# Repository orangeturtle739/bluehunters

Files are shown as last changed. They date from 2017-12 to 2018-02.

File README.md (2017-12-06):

---
title: 'Blue Hunters: Bluetooth RSSI Locator Robots'
subtitle: '_ECE 4760, Fall 2017_'
author:
  - Jacob Glueck ([jng55](mailto:jng55@cornell.edu))
  - Jane Du ([zd53](mailto:zd53@cornell.edu))
  - Justin Cray ([jgc232](mailto:jgc232@cornell.edu))

date: December 6, 2017
---

## Introduction
We built 2 small cars which used Bluetooth Received Signal Strength Indicator (RSSI) measurements to navigate towards a stationary base station.
The cars and base station used a Bluetooth Low Energy (BLE) 4.0 module to take the measurements and a PIC32MX250 microcontroller. The cars also used a 3 axis magnetometer as as compass in order to reliably turn, as well as 2 micro 9 g servos to drive.
Each unit was powered with 3 AA batteries.
Finally, the chassis and wheels of each car were 3D printed.

### Video

<iframe width="560" height="315" src="https://www.youtube.com/embed/g5H4cLJBA_Q?rel=0" frameborder="0" gesture="media" allow="encrypted-media" allowfullscreen></iframe>

## Design
<!-- Explain the approach you used for both software and hardware aspects of the assignment.
Be sure to include the design of tests whose outcome are convincing to the reader
(or to the instructor in the lab) that the requirements of the assignment have been met. -->
<!-- High level design:
rationale and sources of your project idea
background math
logical structure
hardware/software tradeoffs
Relationship of your design to available IEEE, ISO, ANSI, DIN, and other standards.
Discuss existing patents, copyrights, and trademarks which are relevant to your project.
Program/hardware design:
program details. Could someone else build this based on what you have written?
hardware details. Could someone else build this based on what you have written?
Be sure to specifically reference any design or code you used from someone else.
Things you tried which did not work -->

### Chassis

The robots are made from 4 3D printed pieces: 2 wheels, the frame, and the caster in the back.
The servos, a 3 AA battery holder, and a perfboard containing all the circuitry are mounted directly to the frame.

The robots where designed in [OpenSCAD](http://www.openscad.org/), and their source code is available in [our git repository](https://github.com/orangeturtle739/bluehunters/tree/master/cad) and [below](#appendix-b-source-listing).
There are three files, [`frame.scad`](generated/frame.scad.html), [`drag.scad`](generated/drag.scad.html), and [`wheel.scad`](generated/wheel.scad.html), for each of the three parts. The main modules are defined in [`main.scad`](generated/main.scad.html), and the other files just instantiate them. The following renderings show each part:

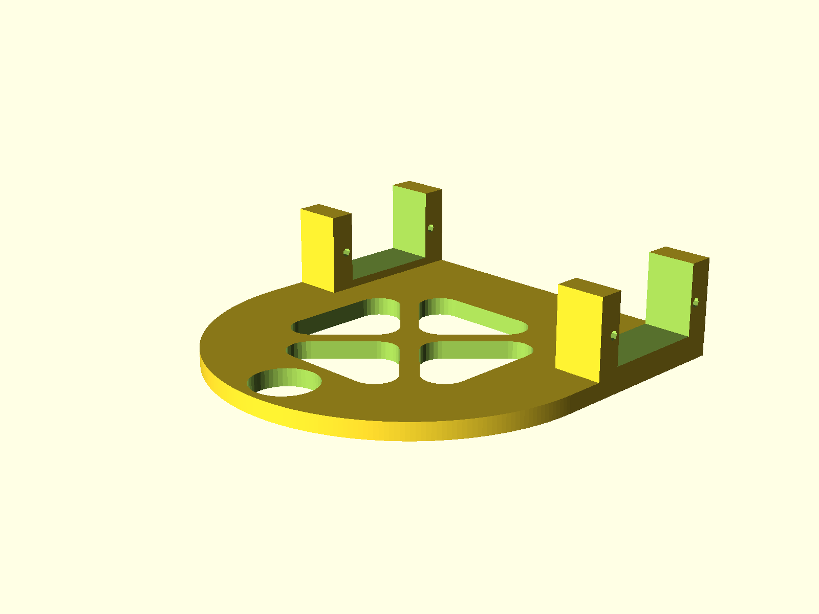
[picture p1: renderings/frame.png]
Robot chassis


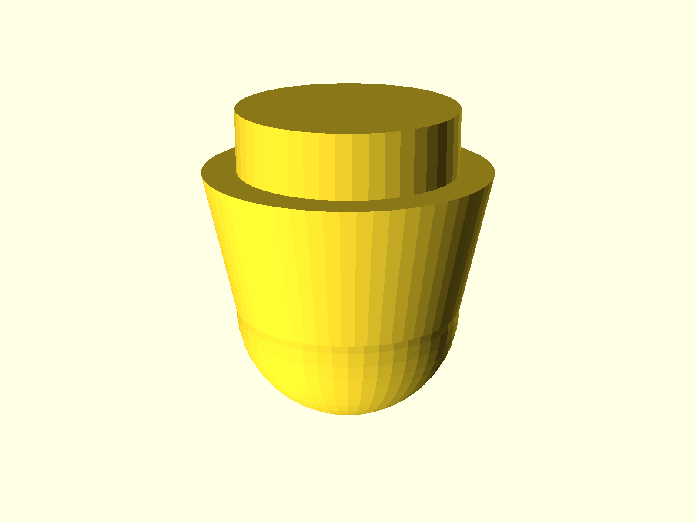
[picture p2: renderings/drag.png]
Caster wheel on back of robot


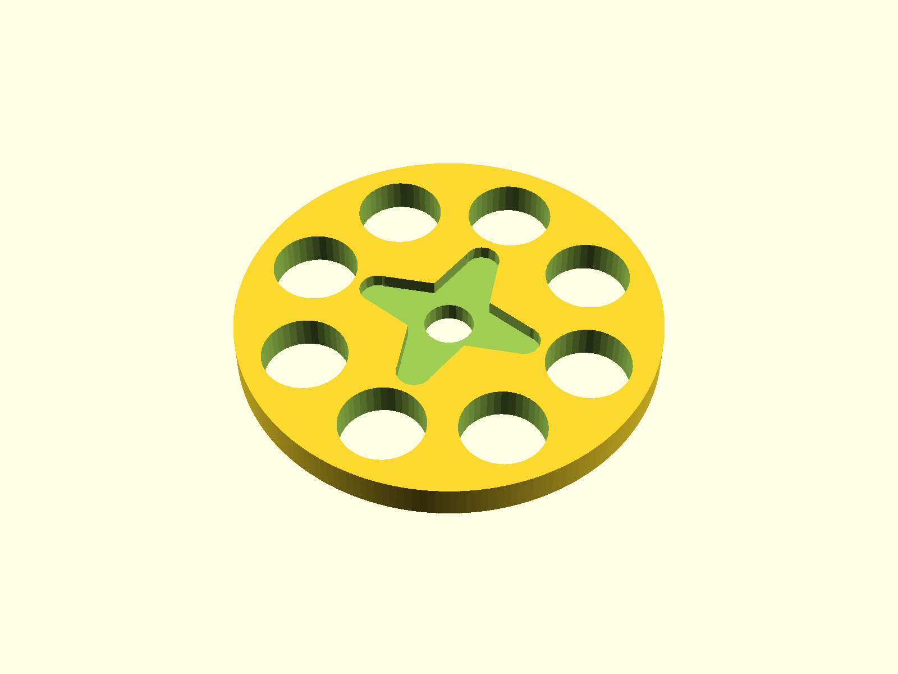
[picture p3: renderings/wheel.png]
Robot wheel


The parts were printed in ABS using [Maker Select 3D Printer v2](https://www.monoprice.com/product?c_id=107&cp_id=10724&cs_id=1072403&p_id=13860&seq=1&format=2) printers. All parts were printed
with a layer height of 0.3 mm, as there was no need for a smooth finish or high tolerances. The parts where sliced with [Cura](https://ultimaker.com/en/products/ultimaker-cura-software).

### Pictures

Full system (base station and 2 robots):

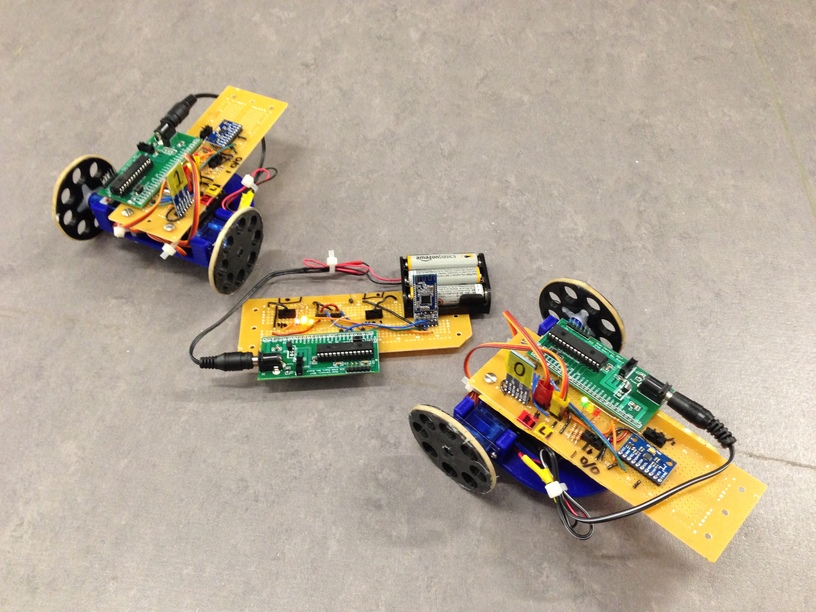
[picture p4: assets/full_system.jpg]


Multiple views of the robots:

------------------------------ ------------------------------
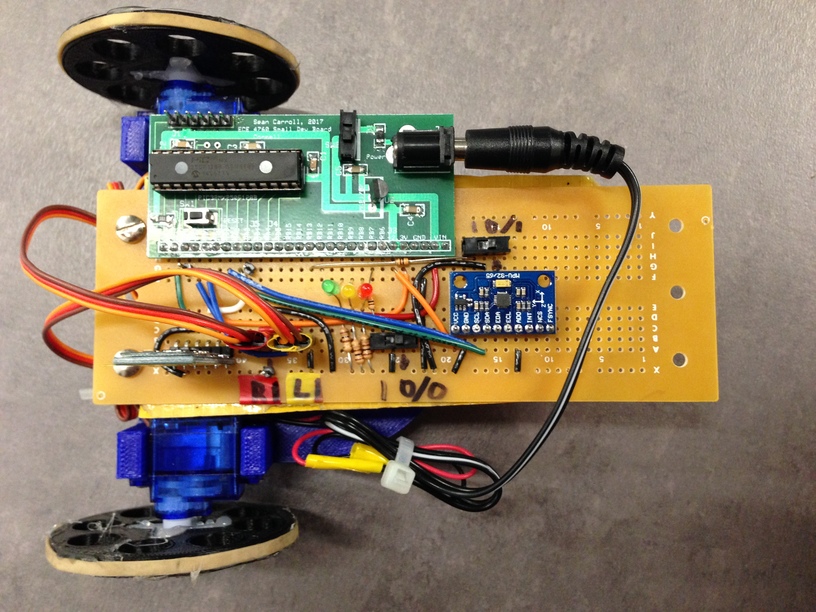
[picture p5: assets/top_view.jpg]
Top view
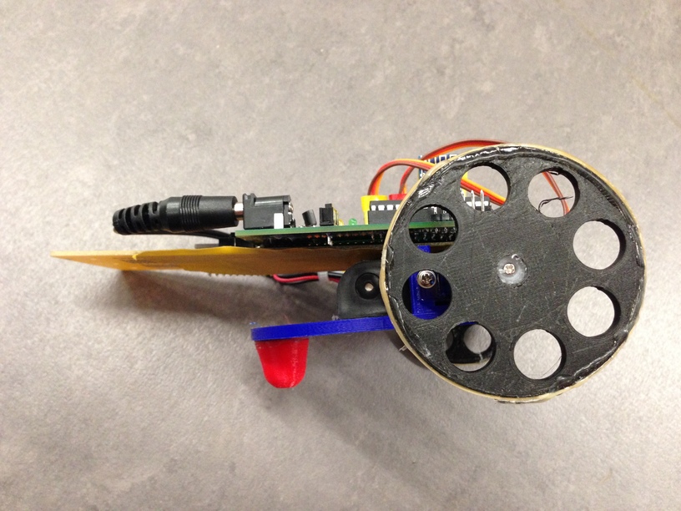
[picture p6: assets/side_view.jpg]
Side view
      
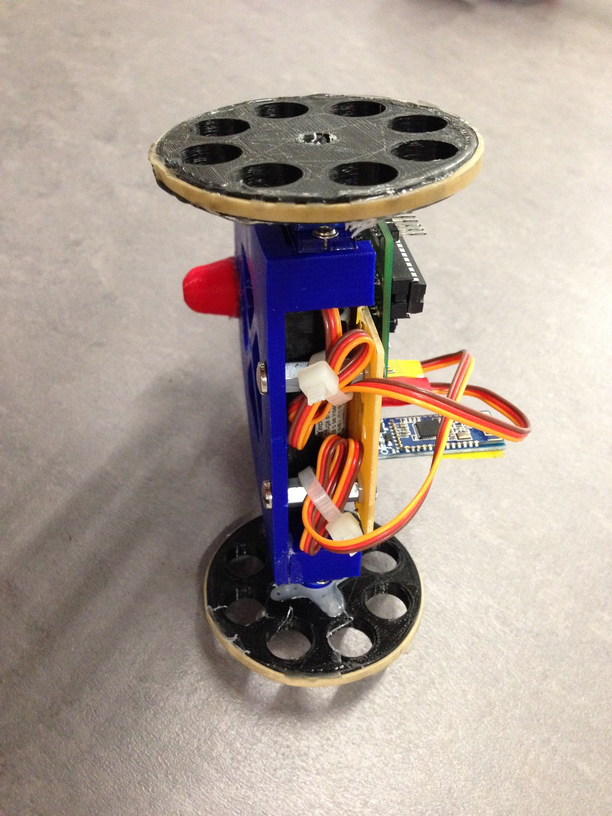
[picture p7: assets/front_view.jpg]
Front view
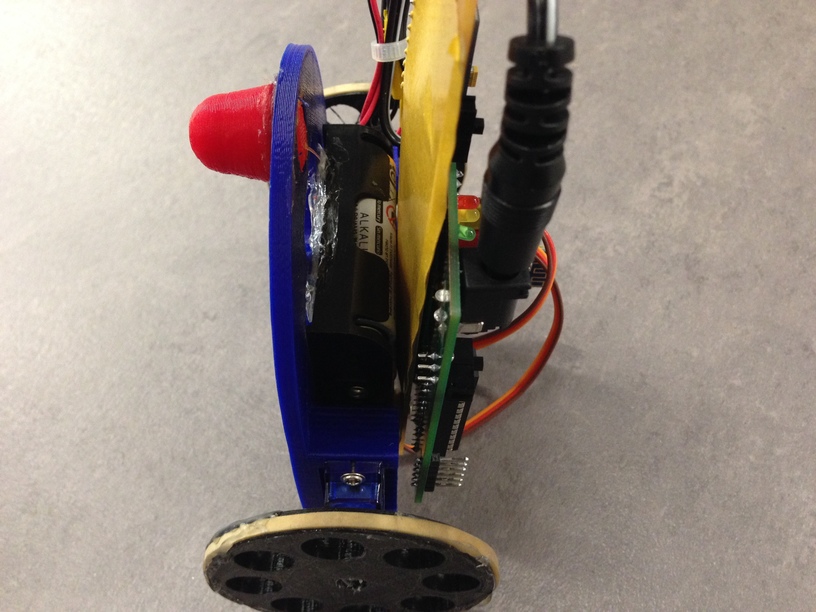
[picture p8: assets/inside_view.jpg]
Inside
  
------------------------------ ------------------------------

### Electronics

#### Bluetooth modules

The HM-10 bluetooth modules we bought off Ebay were fakes: they were not made by Jnhuamao [^china], and did not come with genuine Jnhuamao firmware.
However, they did have real TI CC2541 chips.
We realized they were fakes when they did not behave according to the Jnhuamao data sheet (see [the data sheets section](#data-sheets)).
Luckily, the hardware on the fake chips is the same as that of the genuine chips, minus an external crystal, and the genuine firmware checks for the presence of the crystal, and works even without it. [^arduinoforums]
As such, we reprogrammed the chips with the genuine firmware according to an [Arduino forum post](http://forum.arduino.cc/index.php?topic=393655.msg2709528#msg2709528):

1.  We soldered wires to the programming pins on the breakout boards, and connected those pins to an [Arduino Teensy 3.2](https://www.pjrc.com/teensy/teensy31.html).
    We chose a Teensy because it is 3.3 V as opposed to 5, which would damage the 3.3 V CC2541.

    The pins were connected as follows:

      | Name          | CC2541 Pin | Arduino Pin |
      | ------------- | ---        | ----------- |
      | `DEBUG_CLOCK` | 7          | 5           |
      | `DEBUG_DATA`  | 8          | 6           |
      | `RESET_N`     | 11         | 4           |

    The layout of the HM-10 board is:

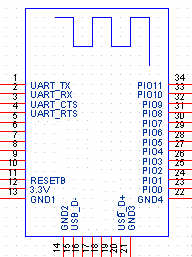
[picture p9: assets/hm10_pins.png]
    
2.  We uploaded the [`CCLoader.ino` sketch](https://github.com/RedBearLab/CCLoader/blob/master/Arduino/CCLoader/CCLoader.ino) to the Arduino.
3.  Finally, we ran (in a Windows virtual machine) [`CCLoader.exe`](https://github.com/RedBearLab/CCLoader/tree/master/Windows).
    This program takes 3 arguments:
    ```bash
    CCLoader.exe <COM Port> <Firmware.bin> 0
    ```
    The firmware file came from the same Arduino form post, and can be found [here](http://forum.arduino.cc/index.php?action=dlattach;topic=393655.0;attach=183702).

There is also an excellent [YouTube video](https://www.youtube.com/watch?v=ez3491-v8Og), which explains the firmware flashing process.

After flashing genuine firmware onto the chip, the next step was to update the firmware to the latest version.
The firmware flashed onto the board was version 540, but Jnhuamao had (at the time we did this project) [released version 603](http://www.jnhuamao.cn/rom/HMSoft-10-2541-V603.zip). [^firmware]
They also provide [instructions on how to upgrade the firmware](http://www.jnhuamao.cn/HowToUpgradeFirmware_en.zip). The basic process is:

1.  Connect the HM-10 module to a computer using a 3.3 V FTDI to USB adapter.
    Then, use PUTTY to establish a serial session (9600 baud, 8N1).
    Send the chip `AT`; if it is connected properly, it will respond with `OK`.
2.  Send the chip `AT+SBLUP` to put it in firmware update mode.
    It will respond with `OK+SBLUP`. Terminate the PUTTY session.
3.  Run the `HMSoft.exe` program distributed in the firmware update download.
    We ran it in a Windows virtual machine because we did not trust it.
4.  Select the proper port and firmware file using the software, and hit "Load Image".
    The software should handle the rest!
5.  To make sure it worked, establish a serial connection again using PUTTY.
    Send `AT+VERS?` to query the chip for version information.

[^china]: Jnhuamao is the company which makes the HM-10 module, along with other Bluetooth modules. Their English website is: <http://www.jnhuamao.cn/bluetooth.asp?id=1>.
[^arduinoforums]: <http://forum.arduino.cc/index.php?topic=393655.msg2709528#msg2709528>.
[^firmware]: Jnhuamao's firmware download page <http://www.jnhuamao.cn/download_rom_en.asp?id=1#>.

### Software

The robots were programmed in C, using the [MPLAB X IDE](http://www.microchip.com/mplab/mplab-x-ide) v4.0, with the [XC32](http://www.microchip.com/mplab/compilers) v1.4 compiler and the [PIC 32 Legacy Peripheral Library (plib)](http://www.microchip.com/SWLibraryWeb/product.aspx?product=PIC32%20Peripheral%20Library). The full source code is available in [our git repository](https://github.com/orangeturtle739/bluehunters/tree/master/ble.X) and [below](#appendix-b-source-listing). The code is divided into 5 main units:

*   [`ble.c`](generated/ble.c.html): contains all the functions for interacting with the BLE device over UART.
*   [`imu.c`](generated/imu.c.html): contains all the functions for interacting with the IMU (which contained the magnetometer) over I2C.
*   [`servo.c`](generated/servo.c.html): contains all the functions for interacting with the servos using PWM.
*   [`main.c`](generated/main.c.html): the main code.
*   [`pt_cornell_1_2_2.c`](generated/pt_cornell_1_2_2.c.html): contains the functions which were originally declared in the protothreads header file.
    However, since they were in the header file, if multiple source files included the header file, there would be linking errors due to duplicate definitions of symbols.
    Moving the protothreads definitions to a separate file resolved this issue.

#### BLE

The BLE module used UART, at 9600 baud 8N1. We used `UART1` on the PIC for communicating with the BLE module, and used `UART2` for communicating with the computer (for debugging).
The BLE files define a series of macros and `PT_THREAD` functions for printing characters and reading lines in a non-blocking fashion using protothreads. All of the `PT_THREAD` functions can be spawned with `PT_SPAWN` to run them.

The [`main.c`](generated/main.c.html) file contains a thread which does all the communication with the Bluetooth chip using these functions. The commands it sends to the chip are:

*   `AT+RESET`: resets the chip to ensure it is in a clean state before receiving other commands.
*   `AT+IBEA1`: enables the iBeacon functionality of the chip (sets it to 1; `AT+IBEA0` would disable it by setting it to 0).
    This allows the chip to be found with an RSSI scan.
    After setting the value, we query it with `AT+IBEA?` and send the result over the other serial port to a computer for debugging.
*   `AT+ROLE0` or `AT+ROLE1`: sets the role to either peripheral (0) or central (1).
    The base station is set to peripheral, and the 2 robots are set to central.
    Peripheral means the device will respond in inquiries from a central device.
    This allows it to be discovered during an RSSI scan.
    After setting the value, we query it with `AT+ROLE?` and send the result over the other serial port to a computer for debugging.
*   `AT+IMME0` or `AT+IMME1`: sets the work state of the device to either actively listening for Bluetooth signals (0), or only acting when it receives a serial command (1).
    Once again, the base station is set to 0: it needs to listen for signals and respond.
    The robots are set to 1, as the chips need to initiate scan requests when they receive the command over serial.
    After setting the value, we query it with `AT+IMME?` and send the result over the other serial port to a computer for debugging.
*   `AT+NAME%s`: sets the name of the chip (which is visible when scanning) to `%s` (For example, `AT+NAMEPIRATE` names the chip `PIRATE`).
    We give all the chips unique names to make debugging easier.
    After setting the value, we query it with `AT+NAME?` and send the result over the other serial port to a computer for debugging.
*   `AT+SHOW3`: configures the device to advertise both its name and RSSI when scanning.
*   `AT+ADDR?`: queries the device for its hardware address. We recorded the hardware device of each chip, as when doing RSSI scans, the results are reported by hardware address.
*   `AT+DISI?`: performed only on the robots, causing a discovery scan. The result of the scan is a bunch of lines of the form:
    ```
    OK+DISC:00000000:00000000000000000000000000000000:0000000000:6832A3801EBE:-080
    ```
    The second to last token, `6832A3801EBE`, is the hardware address of the discovered device, and the last token, `-080`, is the measured RSSI.
    The chip will transmit a line for each device it finds ("line" is a misnomer as it does not separate them with any characters), followed by `OK+DISCE`.

One interesting thing to note about the chip is that commands do not have to end with newlines or carriage returns. However, if sent, the chip will ignore them.

#### IMU
The PIC commmunicates with the IMU via I2C. The IMU includes a breakout board for the QFN MPU-9250 module, which itself includes 2 dies. One contains the 3-axis gyroscope and 3-axis accelerometer, which were not used in this project, and the other die is the AK8963 3-axis magnetometer (compass).

It is connected to the rest of the MPU module via an auxillary I2C bus, so it is not connected to the MPU's  main I2C bus by default. While the accelerometer and gyroscope registers can be read after powering up the IMU, the compass also needs pass-through mode to be enabled on the IMU to make it an accessible slave on the I2C bus.

Some useful functions as defined in [`imu.h`](generated/imu.h.html) are described below:

*   `void imu_init()`: Initializes the MPU-9250, including configuring the chip to allow reading the compass.
*   `int imu_get_heading()`  Returns the heading of the robot as a value between -180 and 180.
    The compasses were not completely calibrated to find magnetic north; it only ensures angles are correct relevant to past headings.
*   `void imu_mag_read_data(int * destination)` Fetches compass readings; saves register values into `destination` in the form `[x, y, z]`.
*   `int angle_diff(int source, int target)` Gets the difference between two angles in degrees to account for discontinuity between -180 and 180 degrees.
*   `int degree(int deg)`: Offsets degree values so that they fall within the range -180 to 180 degrees.

Initializing the IMU involves opening the I2C module, and then configuring the IMU.

1.  We open the `I2C2` module; `I2C1` uses pins already used by the connections to the Bluetooth module.
    We open it with the baud rate generator value `BRG = (Fpb / 2 / baudrate) - 2 = 4e7 / 2 / 4e5 - 2 = 48`, as specified for `OpenI2C2()` in the [peripheral libraries](#references).
2.  Pass through is enabled, interrupts for data ready are enabled, the IMU as an I2C master function is disabled, and the sensor is powered up.

This enables the PIC to talk to the AK8963. The AK8963 has several modes of operation, and the chip must be set to power-down mode before switching to other modes. We read compass values with single measurement mode, as specified below:

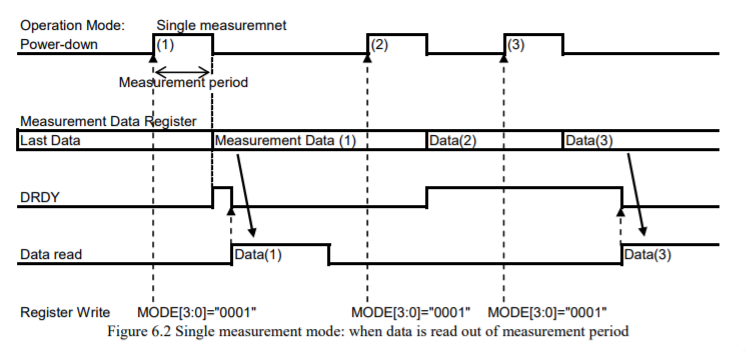
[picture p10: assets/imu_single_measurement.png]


1.  Set the compass to single measurement mode in 14 bit resolution.
2.  Read the 6 data registers (X low, X high, Y low, Y high, Z low, Z high)
3.  Read the Status 2 register to check for magnetic sensor overflow. Without reading this register, the read is not considered complete and further reads will fail.
4.  Wait; if the IMU is read too frequently, it will not have enough time to take measurements.

Additional helper methods used in I2C were defined in [`imu.c`](generated/imu.c.html). These are largely based on the files from the [self-balancing robot](#code-and-designs-borrowed-from-others).

*   `char i2c_read_device(char device, char address)` Reads the data from a single register at `address`
*   `void i2c_write_byte(char device, char address, char data)` All configurations used in this project involved writing single bytes of data.
*   `void i2c_wait(int cnt)` Writes 2 nops; reads require time to return a value, and calling reads consecutively.

In order to calibrate the compass, the robots spun in place when powered on. They recorded the maximum and minimum values for each axes, and used that data to scale and center the magnetometer readings.

#### Servos

For the drive systems, we used the FS90R servos. These servos are continuous rotation servos with a stall torque of 1.5 kg-cm. Continuous rotation servos operate based on PWM duty cycle; since servos operate at a pulse width of 1 to 2 ms out of 20 ms, we used a timer with a prescaler of 32 and a maximum count of 25600, and set the pwm at numbers ranging from 1280 to 2560 (corresponding to the right pulse width).

A 50% duty cycle means the servos are still. A less than 50% duty cycle means the servo turns clockwise and a greater than 50% duty cycle means the servo turns counter-clockwise. To implement the PWM, we use the output capture on the PIC. We set the duty cycle using the built in timers. We set a max and min duty cycle value which were experimentally derived. The middle point is the average of the two. Tank drive is used to control the system where both wheels are driven forward or point turns where one wheel is turned in one direction and one is turned in the other direction. 

#### Protothreads

While the provided protothreads library was very helpful, it did not work correctly when used in multiple compilation units.
The reason for this was that it defined variables and functions in the header file, so if multiple source files included [`pt_cornell_1_2_2.h`](generated/pt_cornell_1_2_2.h.html), linking would fail with duplicate symbol definitions.
Furthermore, if multiple files included [`config_1_2_2.h`](generated/config_1_2_2.h.html), linking would fail with the obscure error:
```
section `.config_BFC00BF4' will not fit in region `config2'
```
This happened because if multiple compilation units included `#pragma config` directives (which they did by including a `#include "config_1_2_2.h"` directive), then the linker would try to assign too many symbols to the configuration region.

The fix to this was twofold:

1.  We modified protothreads to have both a header and source file, with definitions only in the source file.
1.  We only included [`config_1_2_2.h`](generated/config_1_2_2.h.html) in the main C file, and moved all macro definitions to the protothreads header.

The updated versions of protothreads can be found in [Appendix B](#appendix-b-source-listing).

#### Gradient descent

The algorithm for deciding what path to follow is a basic version of gradient descent. The following image represents the decision-making state machine, where the starting state is **Measure rssi twice, take average**.

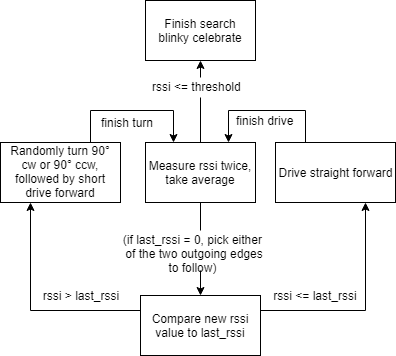
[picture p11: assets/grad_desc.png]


We also implemented and tested the following improved version that allows for correction; a car that has just moved forward and detected a weakened signal does not know whether the beacon to its left or right. If after turning, the signal is still weaker, it has picked the wrong turn. This decision process corrects this (same starting state: **Measure rssi twice, take average**):

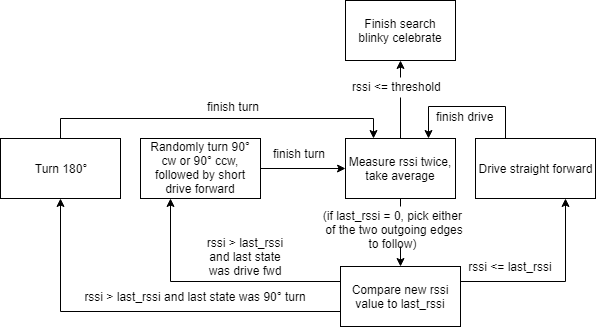
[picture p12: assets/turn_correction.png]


It did not prove much more accurate than randomized gradient descent, largely due to noisy readings from IMU and Bluetooth signal strength. As such, we used the simplified version.

### Testing

#### BLE

Once we flashed the Bluetooth chips with the proper firmware, we used the [LightBlue](https://itunes.apple.com/us/app/lightblue-explorer/id557428110?mt=8) app to test communications.
Using the app, we could discover the Bluetooth chips, and send and receive data.
By initially using a the iPhone app, which was known to work, we could debug the Bluetooth chips in isolation.
Once that worked, we had the chips communicate with each other.
Finally, we had the chips take RSSI measurements.

We also experimented with RSSI, as described in [results](#results). This data validated the effectiveness of RSSI as an approximate metric for distance measurement, though confirmed that it would be highly variable.

#### IMU
- Basic I2C: Basic testing was required to ensure I2C communication with the chip was working. This included testing the correctness of the I2C read and write functions (including the order of starts, restarts, and idles in accordance with the I2C protocol and the chip datasheets), as well basic parameters like the address of the MPU-9250 and its registers.
- Compass I2C: This was more complex, and mostly involved testing the usage of the modes of both the MPU-9250 (IMU module) and the AK8963 (the compass itself). Performance testing was also important here, as the compass would not allow rapid reads in quick succession; we inserted nops in the `imu_mag_read_data(int * destination)` for this reason.
- Compass calibration: We tested incrementally, first using hard-coded maximum and minimum observed values outputted from the IMU, and then with values taken from a self-calibration in which the robot would spin in a circle, and the PIC would record the largest and smallest values it saw on the X- and Y-axes.

#### Servos
We tested the functionality of servo code by testing individual functionality on both the hardware and software side. We tested the servo code in stages, first implementing control at a fixed speed and then implementing directional motion and lastly turning. This allowed us to verify our parts of the code and the functionality of the servos.

#### Whole system
- Some subsystem testing was required for the servo with the IMUs, for turning/driving straight with feedback. We debugged by reading in IMU values via UART and observing the robot's turns.
- We tested extensively with the beacon and two hunters in different environments. Most of our initial testing was in a large, open space with a few metal tables on the periphery. We later tested in the lab in the Digital Lab (Phillips 238), and in the hallway where our demo took place. The confined space of the inside of the lab and hallway, as well as the presence of more reflective bodies (metal doors, tables, people) negatively impacted the performance of our hunters, and it was necessary to recalibrate the hunters to work better in the demo environment.

## Results
<!-- How fast was it? How accurate was it? What were the error ranges? -->
<!--
Results of the design:
This is the section which is most often lacking in student projects. Be specific!
If you took calibration data, then show it!
If you have images or video, include it.
speed of execution (hesitation, filcker, interactiveness, concurrency)
Be quantitative. Show graphs!
accuracy (numeric, music frequencies, video signal timing, etc)
Be quantitative. Show graphs!
how you enforced safety in the design.
interference with other people's designs (e.g. cpu noise, RF interference).
usability by you and other people (perhaps with special needs). -->

In most cases, at least 1 of the 2 robots successfully made it to the base station. However, it was not as reliable as we initially hoped. One of the main reasons for this was the noise in RSSI measurements.

We expected that RSSI would vary with distance according to the following relation:

$\text{RSSI} = A - 10 n \log(d)$

where $A$ and $n$ are RF propagation parameters in dBm, $d$ is distance in meters, and RSSI is the measured RSSI in dBm. [^signalstrength]
We experimented with RSSI measurements to determine how well they worked by taking 2 Bluetooth modules, and measuring the RSSI while changing the distance between them.
One remained stationary on the floor and the other was moved away from it 1 floor tile (each floor tile is a 1 foot square) at a time.
At each point, we took 3 RSSI measurements and averaged them. The graph below displays the results:

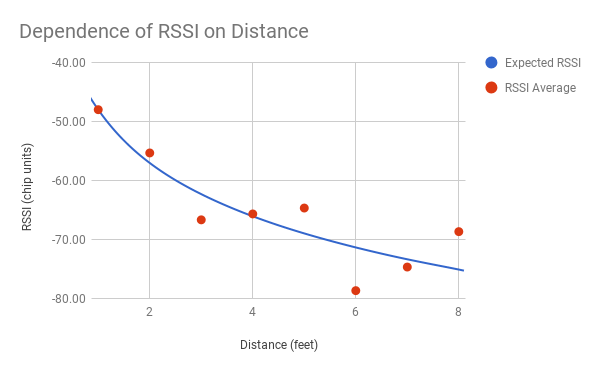
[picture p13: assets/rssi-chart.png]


While the chip reported RSSI in units proportional to dBm, and we measured distances in feet, not meters, we could still use the above formula without worrying about unit conversions.
The constants $A$ and $n$, provided we determined them empirically based on the data, would encode the conversions.
As such, we fit the data using the above formula with $A=-48$ and $n=3$, resulting in the blue curve above.
While the general shape of the curve matches, there is significant noise in the averaged RSSI data.
Furthermore, when we tried to reproduce the measurements, we could not do so precisely -- it seemed to even depend on where our feet where! See [Appendix B](#rssi-data) for the source data for the table.

Despite how noisy the RSSI measurements where, the robots were still able to perform a reasonably accurate gradient descent. In most cases, at least one of the 2 robots would find the beacon in a matter of minutes.

[^signalstrength]: L. Peneda, A. Azenha and A. Carvalho, "Trilateration for indoors positioning within the framework of wireless communications," 2009 35th Annual Conference of IEEE Industrial Electronics, Porto, 2009, pp. 2732-2737.

    doi: 10.1109/IECON.2009.5415423

    URL: <http://ieeexplore.ieee.org/stamp/stamp.jsp?tp=&arnumber=5415423&isnumber=5414636>

## Conclusions
<!-- Useability, what you might have done differently, etc. Any comments concerning the assignment, including suggestions for improvement, excuses, and complaints. -->
<!-- Conclusions:
Analyse your design in terms of how the results met your expectations. What might you do differently next time?
How did your design conform to the applicable standards?
Intellectual property considerations.
Did you reuse code or someone else's design?
Did you use code in the public domain?
Are you reverse-engineering a design? How did you deal with patent/trademark issues.
Did you have to sign non-disclosure to get a sample part?
Are there patent opportunites for your project?
Are there publishing opportunities for your project?
Ethical considerations. Refering to the IEEE Code of Ethics, specifically explain how decisions you made or actions you took in this project were consistent with this Code of Ethics. I expect at least 200 words on this topic. A bulleted list will not be acceptable. -->

This assignment was an interesting exploration into short-range distance determination using Bluetooth, a generally unconventional approach. We were warned beforehand about the difficulties in using Bluetooth RSSI, a measurement particularly susceptible to multipath interference, as a distance sensor -- both in the papers and reference materials researched before implementation, as well as by course staff in the early stages of our project. We worked with the course staff to simplify and stratify our project into workable milestones. Our final project is a reduced version of our original plan.

Our hunting bots worked reliably when they stayed within roughly 1 m of the beacon. After this, they entered the land of shallow gradients: the signal strength from the beacon (already noisy) would not change very much, and often only due to noise. The hunting bots normally could never recover from this. Our bots also worked better in larger, more open spaces, preferably without metal structures like tables or doors nearby. Both of these are reasonable given the operating range of BLE 4.0.

We reused some of the code from the [Self-Balancing Robot](https://people.ece.cornell.edu/land/courses/ece4760/FinalProjects/f2015/dc686_nn233_hz263/final_project_webpage_v2/dc686_nn233_hz263/index.html) as [cited](#code-and-designs-borrowed-from-others) in  our references section, and explained in [IMU](#imu). The rest of the design is ours, and is not an infringement on intellectual property. We also used the Bluetooth firmware flashing technique we discovered on the [Arduino forums](http://forum.arduino.cc/index.php?topic=393655.msg2709528#msg2709528).

We did not reverse-engineer any technology, and did not encounter any issues with trademarks or patents. We did not have to sign non-disclosure to get a sample part. We hope to further polish our findings and report, and will aim to publish them in a print magazine, ideally as a part of ECE 4920.

There are many potential avenues for improvements or further development. In addition to more circumstantial difficulties encountered during the project work period (such as extremely unbalanced servos, where one always ran faster than the other), two areas of potential improvement are as follows:

- *Communication between the two robots*. While Bluetooth may not offer good distance measurement via RSSI, it can be used for reliable communication between modules. It would be straightforward for one hunting robot to inform the other whether it believes it is approaching the beacon or not. In the simplest case, a hunting robot that is approaching, or already at, the beacon can provide a second point of reference for a currently hunting robot.
- *More complete usage of IMU*. A lot of development time was spent simply on getting the PIC to compass communication running, and not much time was spent on calibrating the sensor or processing the data. In further stages of this project, we could continue to work towards dead reckoning of the mobile robots. This, paired with inter-swarm communication, would make for a much more sophisticated and likely much more efficient system. (Of course, this does not resolve the shallow gradients problem -- but it would allow the approach to the beacon to be much faster.)

### IEEE Code of Ethics

Our project, as well as the design and creation project thereof,  adheres to the [IEEE Code of Ethics](https://www.ieee.org/about/ethics.html). The project itself is relatively small and physically self-contained; it did not have any immediate impact on the environment or safety and health of potential users, we the creators, or any others. We chose the project's topic out of interest and for a challenge, without any conflict of interest. Our report is honest and realistic; none of our data is fabricated, and our conclusions reflect our hard findings. We did not accept any form of bribery.

The project investigated the use of an emerging and popular technology (BLE) in a new application (distance sensing). We consistently received and built upon advice from our TAs and professor Bruce Land, and cite the work we used in the basis of our project.

Additionally, neither we nor our project presented any act of discrimination, and our project does not injure others in any way. We assisted our colleagues (both fellow group members and other classmates) when the occasion arose, such as by offering help debugging or lending a spare module before a demo.

Overall, our project complies with the IEEE Policies, 7.8 Code of Ethics.
<!-- in conclusion, we aren't jerks -->

## Appendices

<!-- Appendix with commented program listing
Appendix with schematics (you can download free software from expresspcb.com to draw schematics)
A block diagram is not a schematic.
Appendix with cost details with all part numbers, vendors, and their price. This cost will include components as described in the Budget Considerations section.
Appendix with a list of the specific tasks in the project carried out by each team member.
References you used:
Data sheets
Vendor sites
Code/designs borrowed from others
Background sites/paper -->

### Appendix A: Legal Considerations

*   The group approves this report for inclusion on the course website.
*   The group approves the video for inclusion on the course youtube channel.
*   The TI CC2541 meets FCC CFR47 Part 15 requirements. [^tidatasheet]

[^tidatasheet]: See the top of page 8 of <http://www.ti.com/lit/ds/symlink/cc2541.pdf> for compliance information.

### Appendix B: Source Listing
Our source code can be found [on Github](https://github.com/orangeturtle739/bluehunters).
Each file can also be found below:

#### Code

*   [`ble.c`](generated/ble.c.html)
*   [`ble.h`](generated/ble.h.html)
*   [`imu.c`](generated/imu.c.html)
*   [`imu.h`](generated/imu.h.html)
*   [`servo.c`](generated/servo.c.html)
*   [`servo.h`](generated/servo.h.html)
*   [`pt_cornell_1_2_2.c`](generated/pt_cornell_1_2_2.c.html)
*   [`pt_cornell_1_2_2.h`](generated/pt_cornell_1_2_2.h.html)
*   [`main.c`](generated/main.c.html)
*   [`main.h`](generated/main.h.html)
*   [`config_1_2_2.h`](generated/config_1_2_2.h.html)

#### CAD

##### Sources

*   [`main.scad`](generated/main.scad.html)
*   [`frame.scad`](generated/frame.scad.html)
*   [`wheel.scad`](generated/wheel.scad.html)
*   [`drag.scad`](generated/drag.scad.html)
*   [`concept.scad`](generated/concept.scad.html)

##### STL

*   [`frame.stl`](stl/frame.stl)
*   [`wheel.stl`](stl/wheel.stl)
*   [`drag.stl`](stl/drag.stl)

#### RSSI data

| Distance (feet) | RSSI A | RSSI B | RSSI C | RSSI Average | Expected RSSI |
| --- | --- | --- | --- | --- | --- |
| 1 | -48 | -48 | -48 | -48.00 | -48.00 |
| 2 | -56 | -58 | -52 | -55.33 | -57.03 |
| 3 | -66 | -66 | -68 | -66.67 | -62.31 |
| 4 | -64 | -68 | -65 | -65.67 | -66.06 |
| 5 | -60 | -70 | -64 | -64.67 | -68.97 |
| 6 | -80 | -80 | -76 | -78.67 | -71.34 |
| 7 | -80 | -79 | -65 | -74.67 | -73.35 |
| 8 | -68 | -66 | -72 | -68.67 | -75.09 |

### Appendix C: Schematics

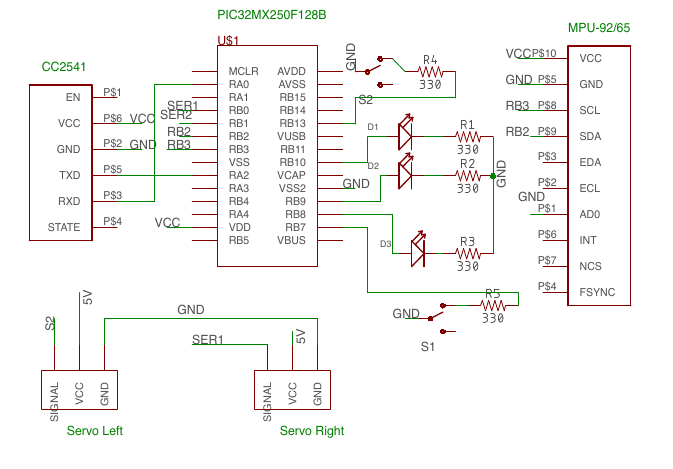
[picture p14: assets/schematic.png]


### Appendix D: Bill Of Materials

| Name | Manufacturer Part Number | Vendor | Vendor Part Number | Quantity | Unit Cost | Total Cost |
|---| ---| ---|---|---|---|---|
| BLE 4.0 Module (TI CC2541) | HM-10 | [Ebay](https://www.ebay.com/itm/AT-09-BLE-Bluetooth-4-0-Uart-Transceiver-Module-CC2541-Central-Switching-HM-10/142425748901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)  | 142425748901  | 3 | $3.99  | $11.97  |
| FEETECH FS90R  (pack of 2) Continuous Rotation Robotic Servo | FS90R  | [Amazon](https://www.amazon.com/gp/product/B074BFQC3Q/ref=oh_aui_detailpage_o06_s00?ie=UTF8&psc=1) | B074BFQC3Q  | 2  | $12.39  | $24.78  |
| HiLetgo 9-Axis 9 DOF 16 Bit Gyroscope Acceleration Magnetic Sensor | MPU-9250  | [Amazon](https://www.amazon.com/HiLetgo-Gyroscope-Acceleration-Accelerator-Magnetometer/dp/B01I1J0Z7Y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)  | B01I1J0Z7Y | 2 | $8.49  | $16.98 |
| Small board | -- | Lab rental | -- | 3 | $5.00 | $15.00 |
| PIC32MX250F128B | PIC32MX250F128B | Lab rental | -- | 3 | $5.00 | $15.00 |
| 6-inch Protoboard | -- | Lab rental | -- | 3 | $2.50 | $7.50 |
| Male header pins | -- | Lab | -- | 129 | $0.05 | $6.45 |

**Total:** $97.68

### Appendix E: Work Distribution

*   **Jacob:**
    *   Bluetooth firmware hacking
    *   Bluetooth UART code
    *   CAD design & 3D printing
*   **Jane:**
    *   I2C IMU code
    *   Robot motion code and gradient descent algorithm
*   **Justin:**
    *   Servo control code
    *   Board assembly (3 small boards and our 3 of our protoboards)
    *   Schematic

### References

#### Data sheets

*   [MPU-9250](https://www.invensense.com/wp-content/uploads/2015/02/PS-MPU-9250A-01-v1.1.pdf) and [its register map](https://cdn.sparkfun.com/assets/learn_tutorials/5/5/0/MPU-9250-Register-Map.pdf).
*   [3-axis Electronic Compass on IMU](https://www.akm.com/akm/en/file/datasheet/AK8963C.pdf).
*   [HM-10 (Bluetooth breakout module & firmware)](http://www.jnhuamao.cn/bluetooth40_en.zip). The ZIP contains the original data sheet, as well as other documentation. [MIT has a PDF](http://fab.cba.mit.edu/classes/863.15/doc/tutorials/programming/bluetooth/bluetooth40_en.pdf) available, which may me out of date, but is easier to get to.
*   [PIC32MX250](http://ww1.microchip.com/downloads/en/DeviceDoc/60001168J.pdf).

#### Code and designs borrowed from others

*   [Self-Balancing Robot](https://people.ece.cornell.edu/land/courses/ece4760/FinalProjects/f2015/dc686_nn233_hz263/final_project_webpage_v2/dc686_nn233_hz263/index.html) by Desmond Caulley (dc686@cornell.edu), Nadav Nehoran (nn233@cornell.edu), Sherry Zhao (hz263@cornell.edu). In particular, we borrowed extensively from their [i2c_helper.h](https://people.ece.cornell.edu/land/courses/ece4760/FinalProjects/f2015/dc686_nn233_hz263/final_project_webpage_v2/dc686_nn233_hz263/dc686_nn233_hz263/i2c_helper.h).

#### Other

* [ECE 4760 Website](http://people.ece.cornell.edu/land/courses/ece4760/) by Bruce Land
* Website template: <https://github.com/tajmone/pandoc-goodies/tree/master/templates/html5/github>.

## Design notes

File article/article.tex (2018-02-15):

\PassOptionsToPackage{unicode=true}{hyperref} % options for packages loaded elsewhere
\PassOptionsToPackage{hyphens}{url}
%
\documentclass[]{article}
\usepackage{lmodern}
\usepackage{amssymb,amsmath}
\usepackage{ifxetex,ifluatex}
\usepackage{fixltx2e} % provides \textsubscript
\usepackage[T1]{fontenc}
\usepackage[utf8]{inputenc}
\usepackage{textcomp} % provides euro and other symbols
% use upquote if available, for straight quotes in verbatim environments
\IfFileExists{upquote.sty}{\usepackage{upquote}}{}
% use microtype if available
\IfFileExists{microtype.sty}{%
\usepackage[]{microtype}
\UseMicrotypeSet[protrusion]{basicmath} % disable protrusion for tt fonts
}{}
\IfFileExists{parskip.sty}{%
\usepackage{parskip}
}{% else
\setlength{\parindent}{0pt}
\setlength{\parskip}{6pt plus 2pt minus 1pt}
}
\usepackage{hyperref}
\hypersetup{
    colorlinks=true,
    linkcolor=blue,
    filecolor=magenta,
    urlcolor=cyan,
}
\urlstyle{same}  % don't use monospace font for urls
\usepackage{color}
\usepackage{fancyvrb}
\newcommand{\VerbBar}{|}
\newcommand{\VERB}{\Verb[commandchars=\\\{\}]}
\DefineVerbatimEnvironment{Highlighting}{Verbatim}{commandchars=\\\{\}}
% Add ',fontsize=\small' for more characters per line
\newenvironment{Shaded}{}{}
\newcommand{\KeywordTok}[1]{\textcolor[rgb]{0.00,0.44,0.13}{\textbf{#1}}}
\newcommand{\DataTypeTok}[1]{\textcolor[rgb]{0.56,0.13,0.00}{#1}}
\newcommand{\DecValTok}[1]{\textcolor[rgb]{0.25,0.63,0.44}{#1}}
\newcommand{\BaseNTok}[1]{\textcolor[rgb]{0.25,0.63,0.44}{#1}}
\newcommand{\FloatTok}[1]{\textcolor[rgb]{0.25,0.63,0.44}{#1}}
\newcommand{\ConstantTok}[1]{\textcolor[rgb]{0.53,0.00,0.00}{#1}}
\newcommand{\CharTok}[1]{\textcolor[rgb]{0.25,0.44,0.63}{#1}}
\newcommand{\SpecialCharTok}[1]{\textcolor[rgb]{0.25,0.44,0.63}{#1}}
\newcommand{\StringTok}[1]{\textcolor[rgb]{0.25,0.44,0.63}{#1}}
\newcommand{\VerbatimStringTok}[1]{\textcolor[rgb]{0.25,0.44,0.63}{#1}}
\newcommand{\SpecialStringTok}[1]{\textcolor[rgb]{0.73,0.40,0.53}{#1}}
\newcommand{\ImportTok}[1]{#1}
\newcommand{\CommentTok}[1]{\textcolor[rgb]{0.38,0.63,0.69}{\textit{#1}}}
\newcommand{\DocumentationTok}[1]{\textcolor[rgb]{0.73,0.13,0.13}{\textit{#1}}}
\newcommand{\AnnotationTok}[1]{\textcolor[rgb]{0.38,0.63,0.69}{\textbf{\textit{#1}}}}
\newcommand{\CommentVarTok}[1]{\textcolor[rgb]{0.38,0.63,0.69}{\textbf{\textit{#1}}}}
\newcommand{\OtherTok}[1]{\textcolor[rgb]{0.00,0.44,0.13}{#1}}
\newcommand{\FunctionTok}[1]{\textcolor[rgb]{0.02,0.16,0.49}{#1}}
\newcommand{\VariableTok}[1]{\textcolor[rgb]{0.10,0.09,0.49}{#1}}
\newcommand{\ControlFlowTok}[1]{\textcolor[rgb]{0.00,0.44,0.13}{\textbf{#1}}}
\newcommand{\OperatorTok}[1]{\textcolor[rgb]{0.40,0.40,0.40}{#1}}
\newcommand{\BuiltInTok}[1]{#1}
\newcommand{\ExtensionTok}[1]{#1}
\newcommand{\PreprocessorTok}[1]{\textcolor[rgb]{0.74,0.48,0.00}{#1}}
\newcommand{\AttributeTok}[1]{\textcolor[rgb]{0.49,0.56,0.16}{#1}}
\newcommand{\RegionMarkerTok}[1]{#1}
\newcommand{\InformationTok}[1]{\textcolor[rgb]{0.38,0.63,0.69}{\textbf{\textit{#1}}}}
\newcommand{\WarningTok}[1]{\textcolor[rgb]{0.38,0.63,0.69}{\textbf{\textit{#1}}}}
\newcommand{\AlertTok}[1]{\textcolor[rgb]{1.00,0.00,0.00}{\textbf{#1}}}
\newcommand{\ErrorTok}[1]{\textcolor[rgb]{1.00,0.00,0.00}{\textbf{#1}}}
\newcommand{\NormalTok}[1]{#1}
\usepackage{longtable,booktabs,multirow}
\usepackage{tabularx}
\newcommand{\ra}[1]{\renewcommand{\arraystretch}{#1}}

% Fix footnotes in tables (requires footnote package)
\IfFileExists{footnote.sty}{\usepackage{footnote}\makesavenoteenv{longtable}}{}
\usepackage{graphicx,grffile}
\graphicspath{{../assets/}{../renderings/}{../schematics/}}
\usepackage{subfig}
\usepackage[page]{appendix}
\makeatletter
\def\maxwidth{\ifdim\Gin@nat@width>\linewidth\linewidth\else\Gin@nat@width\fi}
\def\maxheight{\ifdim\Gin@nat@height>\textheight\textheight\else\Gin@nat@height\fi}
\makeatother
% Scale images if necessary, so that they will not overflow the page
% margins by default, and it is still possible to overwrite the defaults
% using explicit options in \includegraphics[width, height, ...]{}
\setkeys{Gin}{width=\maxwidth,height=\maxheight,keepaspectratio}
\setlength{\emergencystretch}{3em}  % prevent overfull lines
\providecommand{\tightlist}{%
  \setlength{\itemsep}{0pt}\setlength{\parskip}{0pt}}
\setcounter{secnumdepth}{0}
% Redefines (sub)paragraphs to behave more like sections
\ifx\paragraph\undefined\else
\let\oldparagraph\paragraph
\renewcommand{\paragraph}[1]{\oldparagraph{#1}\mbox{}}
\fi
\ifx\subparagraph\undefined\else
\let\oldsubparagraph\subparagraph
\renewcommand{\subparagraph}[1]{\oldsubparagraph{#1}\mbox{}}
\fi

\title{Blue Hunters: Bluetooth RSSI Locator Robots}
\author{Jacob Glueck (\href{mailto:jng55@cornell.edu}{jng55}) \and Jane Du (\href{mailto:zd53@cornell.edu}{zd53}) \and Justin Cray (\href{mailto:jgc232@cornell.edu}{jgc232})}
\date{December 6, 2017}

\begin{document}
\maketitle

\hypertarget{introduction}{%
\subsection{Introduction}\label{introduction}}

Navigating through a plane is a problem with many diverse applications and solutions. We explore the approach of letting a robot use the strength of a broadcasted signal to locate itself. In particular, we investigate using the Received Signal Strength Indicator (RSSI) of Bluetooth Low Energy (BLE) 4.0 chips to allow wheeled mobile robots to navigate towards a stationary base station. The robot detects its proximity to the station based on the strength of the signal and moves towards what it believes to be the signal source. 

In the process of designing and building the hunting robots and the beacon, we encountered an interesting challenge in particular: fake Bluetooth modules from non-official vendors with usable hardware but out-of-date (and poorly documented) firmware. We explain the process we used to find, flash, and verify the correct firmware in order to use it for our project.

Each robot was controlled by a PIC32MX250 microcontroller, and used a 3 axis magnetometer as as compass in order to reliably turn, as well as 2 micro 9 g servos to drive.
Each unit was powered with 3 AA batteries.
Finally, the chassis and wheels of each car were 3D printed.
Figure \ref{fig:robotsystem} shows the entire system.

\begin{figure}
  \centering
  
  \caption{Full system with 2 robots and the base station}
  \label{fig:robotsystem}
\end{figure}

\subsection{Design}

The design of the robots and beacon can be split into 3 rough categories: first, the construction of the robot itself, including the design of the chassis; second, the integration of the bluetooth modules that were used to transmit and receive signals, and lastly, the algorithm and sensors used by the robot to orient itself and move towards the source of the signal.

\subsubsection{Robot Construction}

The system consists of 2 robots, and a base station.
We designed the robots to be small, light, and maneuverable.
Each robot has 2 wheels, driven by a 9 gram micro servo, as well as a third round plastic leg, serving as a caster wheel.
We 3D printed the robot's frame in ABS, resulting in an easy to assemble robot.
After printing the parts, we mounted a 3 AA battery pack to the frame to provide power,
and screwed in a perfboard on standoffs. See \ref{fig:robotchassis} for the parts in each robot.

\begin{figure}
  \centering
  \subfloat[Frame] {
    
    \label{fig:robotfrane}
  }
  \subfloat[Wheel]{
    
    \label{fig:robotwheel}
  }
  \\
  \subfloat[Caster]{
    
    \label{fig:robotcaster}
  }
  \caption{Components of robot chassis}
  \label{fig:robotchassis}
\end{figure}

The electronics for each robot consisted of 4 main components: a PIC32MC250F128B microcontroller, a MPU-9250 IMU with a 3 axis gryoscope, accelerometer, and magnetometer, a HM-10 BLE module with a Texas Instruments CC2541 chip, and two 9 gram FS90R micro continuous rotation servos.
The BLE module connected to the PIC through a UART connection, and the IMU connected to the PIC through an I2C bus.
The base station was identical to the robots, minus the IMU and servos.
The HM-10 Bluetooth module was mounted perpendicular to the breadboard, sticking up in the air to hopefully improve the performance of the radio. Figure \ref{fig:schematic} provides a full schematic for one of the robots.

\begin{figure}
  \centering
  \subfloat[] {
    
    \label{fig:schematic-robot}
  }
  \\
  \subfloat[] {
    
    \label{fig:schematic-sdb}
  }
  \caption{Schematic}
  \label{fig:schematic}
\end{figure}

While trying to use the Bluetooth modules (which we bought off Ebay), we discovered that they didn't adhere to the data sheet \cite{jnhuamaodatasheet}, and after doing some research, concluded they were fake!
While the boards still had TI CC2541 chips, the firmware they were running was not the genuine Jnhuamao firmware.
Luckily, the only difference between the fake boards and the genuine boards was that then genuine boards had an external crystal, but the genuine firmware checks for the presence of the crystal, and works even without it. \cite{crystal}
Because of that, we were able to salvage the fake chips by reprogramming them with genuine firmware according to an Arduino Fourm post \cite{crystal}.
Essentially, we connected the fake chips to an Arduino Teensy (which is 3.3 volts, and so won't damage the 3.3 volt CC2541) as indicated in table \ref{table:progpins}, using the schematic in figure \ref{fig:hm10} for reference.

\begin{table}[]
  \centering
  \begin{tabular}{@{}lll@{}}
    \toprule
    Name & CC2541 Pin & Arduino Pin\tabularnewline
    \midrule
    \texttt{DEBUG\_CLOCK} & 7 & 5\tabularnewline
    \texttt{DEBUG\_DATA} & 8 & 6\tabularnewline
    \texttt{RESET\_N} & 11 & 4\tabularnewline
    \bottomrule
  \end{tabular}
  \caption{Arduino to CC2541 pin connections for programming.}
  \label{table:progpins}
\end{table}

\begin{figure}
  \centering
  
  \caption{HM-10 module pin layout \cite{crystal}}
  \label{fig:hm10}
\end{figure}

Then, we uploaded the \texttt{CCLoader.ino} \cite{ccloader} sketch to the Arduino.
This sketch bit bangs the programming signals for the CC2541/
Finally, we ran (in a Windows virtual machine, due to the dubious origin of the software) \texttt{CCLoader.exe} \cite{ccloaderexe}:
\begin{Verbatim}[gobble=2]
  CCLoader.exe <COM Port> <Firmware.bin> 0
\end{Verbatim}
The firmware file came from the Arduino forum post. \cite{firmwarefile}

Next, we updated the chips firmware from from 540, the version we just flashed onto it, to the latest (at the time we did this project) released version, 603. \cite{jnhuamao603}
We connected the HM-10 module to a computer using a 3.3 V FTDI to USB adapter.
Then, using PUTTY established a serial connection (9600 baud, 8N1) and sent the chip \texttt{AT}. If it is connected properly, it will respond with \texttt{OK}.
Next, send the chip \texttt{AT+SBLUP} to put it in firmware update mode.
It will respond with \texttt{OK+SBLUP}. Terminate the PUTTY session.
Run the \texttt{HMSoft.exe} program distributed in the firmware update download.
(Again in a Windows virtual machine, due to the dubious origin of the software.)
Select the proper port and firmware file using the software, and hit ``Load Image''.
The software should handle the rest!
To make sure it worked, establish a serial connection again using PUTTY.
Send \texttt{AT+VERS?} to query the chip for version information.

% \cite{jnhuamaoinstructions}

At this point, we finally had the bluetooth chips in a working state.
In order to have them measure signal strength, we sent it the sequence of commands
shown in table \ref{table:blecommands} in order to obtain a signal strength measurement.
One interesting thing to note about the chip is that commands do not have to end with newlines or carriage returns.
However, if sent, the chip will ignore them.

\begin{table}[]
\centering
\ra{1.3}
\caption{HM-10 Bluetooth module signal strength measurement commands}
\label{table:blecommands}
\begin{tabularx}{\textwidth}{@{}l X@{}}
\toprule
Command & Description \\ \midrule
\texttt{AT+RESET} & Resets the chip to ensure it is in a clean state
before receiving other commands. \\

\texttt{AT+IBEA1} & Sets the iBeacon functionality of the chip (1 on, 0 off).
This allows the chip to be found with an RSSI scan. \\

\texttt{AT+ROLE\{0|1\}} & Sets the role to either peripheral (0) or central (1).
The base station is set to peripheral, and the 2 robots are set to central.
Peripheral means the device will respond in inquiries from a central device.
This allows it to be discovered during an RSSI scan.\\

\texttt{AT+IMME\{0|1\}} & Sets the work state of the device to either actively
listening for Bluetooth signals (0), or only acting when it receives a serial
command (1). Once again, the base station is set to 0: it needs to listen for
signals and respond. The robots are set to 1, as the chips need to initiate scan
requests when they receive the command over serial. \\

\texttt{AT+NAME\{str\}} & Sets the name of the chip (which is visible when
scanning) to the string \texttt{str} (For example, \texttt{AT+NAMEPIRATE} names
the chip \texttt{PIRATE}). We give all the chips unique names to make
debugging easier. \\

\texttt{AT+SHOW3} & Configures the device to advertise both its name
and RSSI when scanning. \\

\texttt{AT+ADDR?} & Queries the device for its hardware address. We
recorded the hardware device of each chip, as when doing RSSI scans,
the results are reported by hardware address. \\

\texttt{AT+DISI?} & Performed only on the robots, causing a discovery
scan. The result of the scan is a series of lines of the form:
{\begin{align*}
&\mathtt{OK+DISC:00000000:00000000000000000000000000000000:}\\
&\mathtt{  0000000000:6832A3801EBE:-080}
\end{align*}}
The second to last token, \texttt{6832A3801EBE}, is the hardware
address of the discovered device, and the last token, \texttt{-080},
is the measured RSSI. The chip will transmit a line for each device it
finds (``line'' is a misnomer as it does not separate them with any
characters), followed by \texttt{OK+DISCE}. \\
\bottomrule
\end{tabularx}
\end{table}

Once we had the Bluetooth signal strength working, we configured the IMU,
a QFN MPU-9250 \cite{mpu9250datasheet} \cite{mpu9250regmap} module.
It has 2 dies: one is the AK8963 3-axis magnetometer \cite{ak8963cdatasheet},
and the other contains the 3-axis gyroscope and 3-axis accelerometer, which we did not use.

The microcontroller communicates with the IMU via I2C, and the compass is connected to the rest of the MPU module via an auxiliary I2C bus. For communication between the microcontroller and the AK8963's main die, we based our work off of basic I2C functions from another ECE 4760 project, the Self-Balancing Robot \cite{selfbalancingrobot}. In particular, their \texttt{i2c\_helper.h} was very helpful.

For communication with the actual magnetometer, we needed to configure the IMU to set the compass must as a slave on the I2C bus. For this, it was necessary to enable pass-through mode on the IMU during its configuration.

The AK8963 has several modes of operation, and the chip must be set to power-down mode before switching to other modes.
We read compass values with single measurement mode, as in figure \ref{fig:imu_single_measurement}.

A single compass read involves setting the compass to single measurement mode in 14 bit resolution, reading the 6 data registers (X low, X high, Y low, Y high, Z low, Z high), reading the Status 2 register to check for magnetic sensor overflow (without reading this register, the read is not considered complete and further reads will fail), and finally waiting to ensure that the IMU is not read too frequently, in which case it will not have enough time to take measurements.

\begin{figure}
  \centering
  
  \caption{IMU single measurement mode}
  \label{fig:imu_single_measurement}
\end{figure}

In order to calibrate the compass, the robots spun in place when powered
on. They recorded the maximum and minimum values for each axes, and used
that data to scale and center the magnetometer readings.

\subsubsection{Navigation}

Once we had the robots working, we turned to the algorithm.
Since they don't have much data -- only the last couple signal strength measurements --
we decided to use a simple gradient descent algorithm.
Figure \ref{fig:graddesc} shows 2 versions of the gradient descent algorithm.

\begin{figure}
  \centering
  \subfloat[Simple gradient descent]{
    
    \label{fig:simplegrad}
  }
  \subfloat[Compensating gradient descent]{
      
    \label{fig:compensatinggrad}
  }
  \caption{2 gradient descent algorithms. The initial state is \emph{measure RSSI twice, take average}.}
  \label{fig:graddesc}
\end{figure}

The purpose of the compensating algorithm (figure \ref{fig:compensatinggrad}) was to allow the robots to recover faster after taking a wrong turn: if a robot just just moved forward and detected a weaker signal, turned, and still detected a weaker signal, then it must have turned the wrong way, so it does a 180.
However, it did not prove any more accurate than randomized gradient descent, largely due to noisy RSSI readings.
As such, we used the simplified version.

\subsection{Results}

On average, when starting from 1 meter away, the robots successfully made it to the base station 80\% of the time,
within an average time of 126 seconds.
This wasn't as reliable, or as fast, as we initially hoped.
One of the main reasons for this was the noise in RSSI measurements.

We expected that RSSI would vary with distance according to equation \ref{eq:rssi}:
\begin{equation} \label{eq:rssi}
  \text{RSSI} = A - 10 n \log(d),
\end{equation}
where $A$ and $n$ are RF propagation parameters in dBm, $d$ is distance in meters, and RSSI is the measured RSSI in dBm. \cite{5415423}
We experimented with RSSI measurements to determine how well they worked by taking 2 Bluetooth modules, and measuring the RSSI while moving them apart.
One remained stationary on the floor and the other was moved away from it 1 foot at a time.
At each point, we took 3 RSSI measurements and averaged them. Figure \ref{fig:rssiplot} shows the results (the original data is in table \ref{table:rssidata}).

\begin{figure}
  \centering
  
  \caption{Plot showing bluetooth RSSI as a function of distance}
  \label{fig:rssiplot}
\end{figure}

\begin{table}
  \centering
  \begin{tabular}[]{@{}llllll@{}}
  \toprule
  Distance (feet) & RSSI A & RSSI B & RSSI C & RSSI Average & Expected
  RSSI \\
  \midrule
  1 & -48 & -48 & -48 & -48.00 & -48.00 \\
  2 & -56 & -58 & -52 & -55.33 & -57.03 \\
  3 & -66 & -66 & -68 & -66.67 & -62.31 \\
  4 & -64 & -68 & -65 & -65.67 & -66.06 \\
  5 & -60 & -70 & -64 & -64.67 & -68.97 \\
  6 & -80 & -80 & -76 & -78.67 & -71.34 \\
  7 & -80 & -79 & -65 & -74.67 & -73.35 \\
  8 & -68 & -66 & -72 & -68.67 & -75.09 \\
  \bottomrule
  \end{tabular}
  \caption{RSSI and distance data}
  \label{table:rssidata}
\end{table}

\begin{table}[]
\centering
\ra{1.3}
\caption{Convergence performance of the robots}
\label{table:convergence}
\begin{tabular}{@{}lllllll@{}}
\toprule
\multirow{2}{*}{Trial} & \multicolumn{3}{c}{Robot 0}       & \multicolumn{3}{c}{Robot 1}      \\ \cmidrule(l){2-4} \cmidrule(l){5-7}
                       & Time (s)  & Distance (cm) & Start & Time (s) & Distance (cm) & Start \\ \midrule
1                      & 213       & 53            & South & 94       & 22            & North \\
2                      & \emph{Timeout} & 420           & South & 153      & 36            & North \\
3                      & 308       & 19            & South & 105      & 36            & North \\
4                      & \emph{Collision} & 340           & South & 80       & 20            & North \\
5                      & \emph{Collision} & 240           & South & 92       & 30            & North \\
6                      & 179       & 46            & North & 117      & 20            & South \\
7                      & 56        & 45            & North & 162      & 24            & South \\
8                      & 59        & 27            & North & 197      & 26            & South \\
9                      & 59        & 19            & North & 79       & 30            & South \\
10                     & \emph{Collision} & 231           & North & 67       & 23            & South \\ \bottomrule
\end{tabular}
\end{table}

\begin{table}[]
\centering
\ra{1.3}
\caption{Average convergence behavior}
\label{table:averagecon}
\begin{tabular}{@{}lll@{}}
\toprule
                       & Robot 0        & Robot 1     \\ \midrule
Convergence time (s)   & 146            & 115         \\
Convergence rate       & 60 \%          & 100 \%      \\
Final distance (cm)    & 35             & 27          \\
Failure distance (cm)  & 308            & --          \\ \bottomrule
\end{tabular}
\end{table}

While the chip reported RSSI in units proportional to dBm, and we
measured distances in feet, not meters, we could still use the above
formula without worrying about unit conversions. The constants $A$ and
$n$, provided we determined them empirically based on the data, would
encode the conversions. As such, we fit the data using the above formula
with $A=-48$ and $n=3$, resulting in the blue curve above. While the
general shape of the curve matches, there is significant noise in the
averaged RSSI data. Furthermore, when we tried to reproduce the
measurements, we could not do so precisely -- it seemed to even depend
on where our feet where!

Despite the noise in the RSSI readings, the robots did surprisingly well.
We tested the robots by starting the both 1 meter from the base station,
one on the north side, and one on the south side.
After they started, we timed the amount of time it took them to arrive
at the base station and flash their LEDs.
We set a timeout of 5 minutes, at which point we would measure the
distance between the robot and the base station.
We also measured the distance when the robot arrived.
All distances were measured between the Bluetooth modules.
The results of this are displayed in table \ref{table:convergence},
with averages in table \ref{table:averagecon}.

There are some interesting patterns in the data.
One obvious one is that robot 1 always made it,
while robot 0 only had a 60\% success rate.
In addition, when robot 1 made it, it was on average 8 centimeters
closer than robot 0, and converged about 30 seconds faster!
We think that perhaps the antennas on each had different sensitivities,
as both used the same RSSI threshold for stopping once they reached the goal.
Another interesting result is that when robot 0 failed, it was
on average 3 meters away -- far off in the land of shallow gradients.
The only way to recover from that was dumb luck, as the signal would have been
dominated by noise that far away.

\subsection{Conclusions}

This project was an interesting exploration into short-range distance
determination using Bluetooth, a generally unconventional approach.
We knew that Bluetooth RSSI would be noisy, mostly due to multipath interference and the presence of multiple transmitters in testing environments.
The robots worked reliably when they stayed within roughly 1 meter of the beacon.
After this, they entered the land of shallow gradients:
the signal strength from the beacon (already noisy) would not change very
much, and often only due to noise.
They normally could never recover from this.

There are many potential avenues for improvements or further
development.

Firstly, \emph{communication between the two robots}: while Bluetooth may not offer good distance measurement via RSSI, it can be used for reliable  communication between modules.
It would be straightforward for one hunting robot to inform the other whether it believes it is approaching the beacon or not.
In the simplest case, a robot that is approaching, or already at, the beacon can provide a second point of reference for a currently hunting robot.

Also, \emph{more complete usage of IMU}: additional usage of the accelerometer and gyroscope, coupled with feedback from the servos, would allow the robots to maintain a dead-reckoning position estimate.
This, paired with inter-swarm communication, would make for a much more sophisticated and likely much more efficient system.
(Of course, this does not resolve the shallow gradients problem -- but it would allow the approach to the beacon to be much faster.)

\bibliography{references}{}
\bibliographystyle{ieeetr}

\end{document}

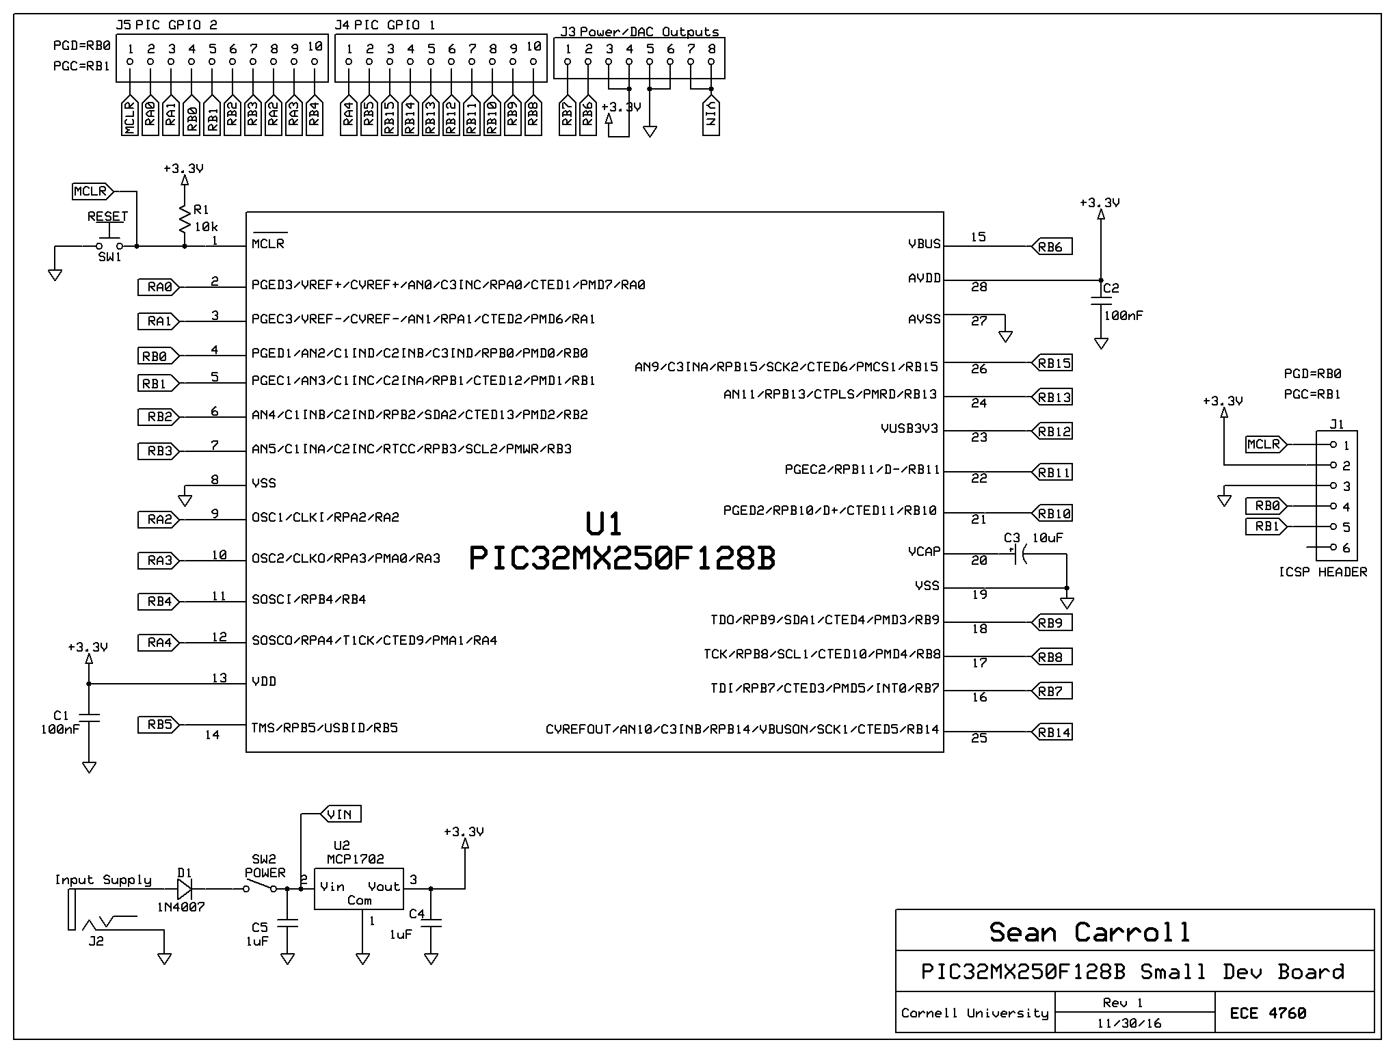
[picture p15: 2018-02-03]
schematics/bluehunters-sdb.png

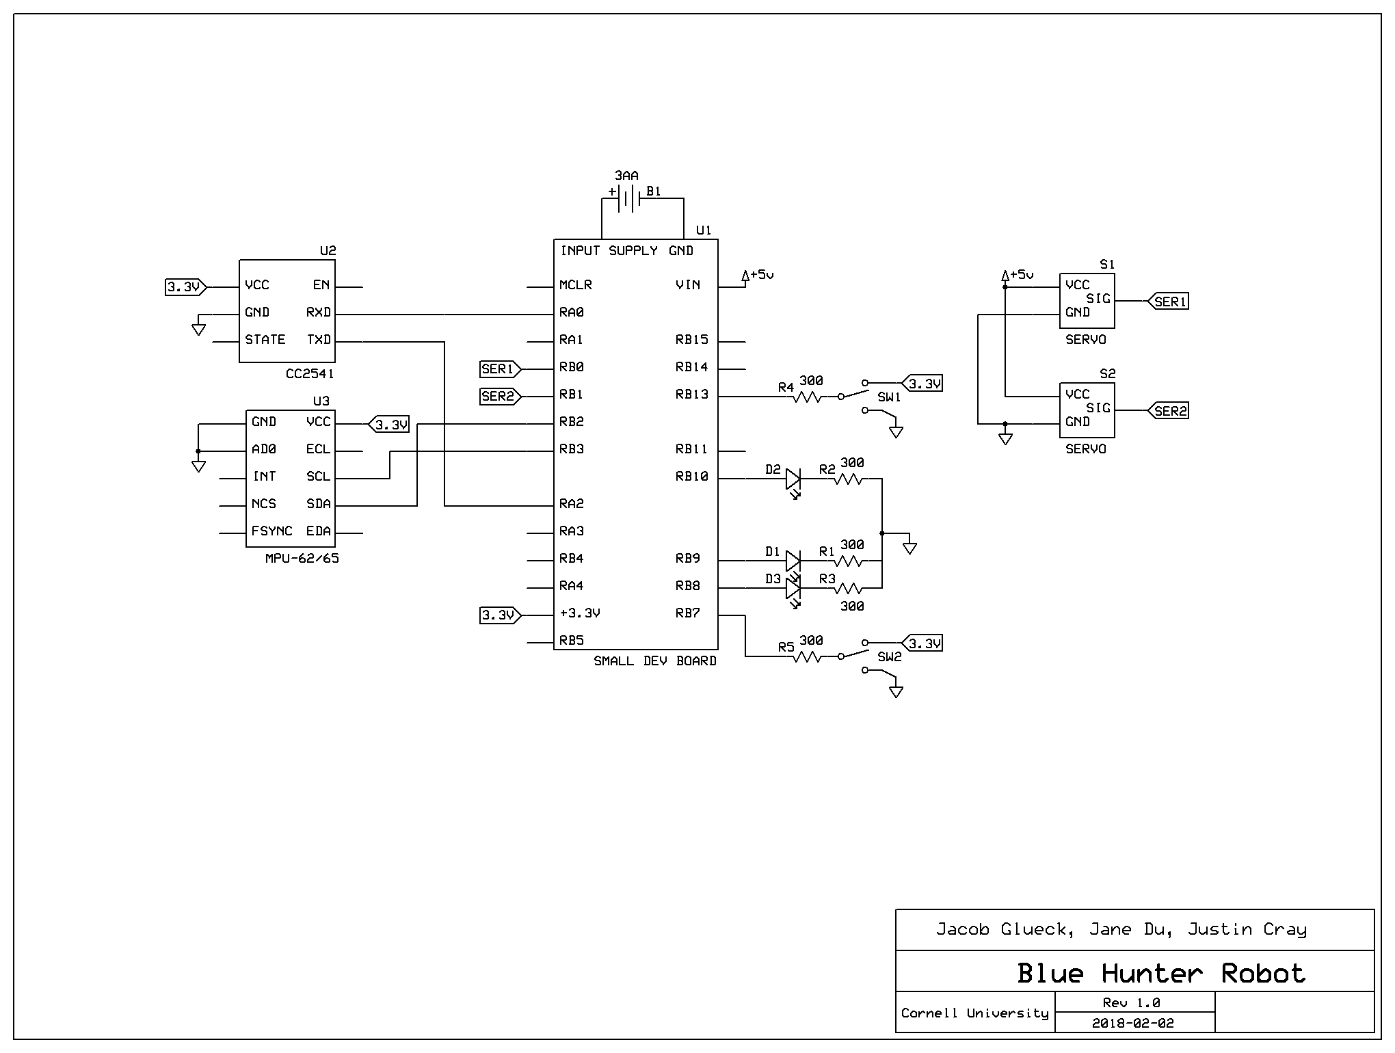
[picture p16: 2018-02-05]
schematics/bluehunters-robot.bmp

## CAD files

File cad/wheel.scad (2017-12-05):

use <main.scad>;

wheel();

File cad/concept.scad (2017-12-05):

$fa = 1;

color("white", 1) {
    union() {
        translate([0,0,-50]) cylinder(h=200, r=400, center=true);
        translate([0,-200,-50]) cube(size=[800,400,200], center=true);
    }

}

color("blue", 1) {
    translate([400 + 50, 0, -100]) {
        rotate([0, 90, 0]) {
            cylinder(h=100, r=200, center=true);
        }
    }
    translate([-(400 + 50), 0, -100]) {
        rotate([0, 90, 0]) {
            cylinder(h=100, r=200, center=true);
        }
    }
}

color("yellow", 1) {
    union() {
        translate([0, -350, -200]) {
            cylinder(h=100, r=50, center=true);
        }
        translate([0, -350, -250]) {
            sphere(r=50, center=true);
        }
    }
}

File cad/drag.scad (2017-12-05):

use <main.scad>;

drag();

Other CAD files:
cad/frame.scad
cad/main.scad

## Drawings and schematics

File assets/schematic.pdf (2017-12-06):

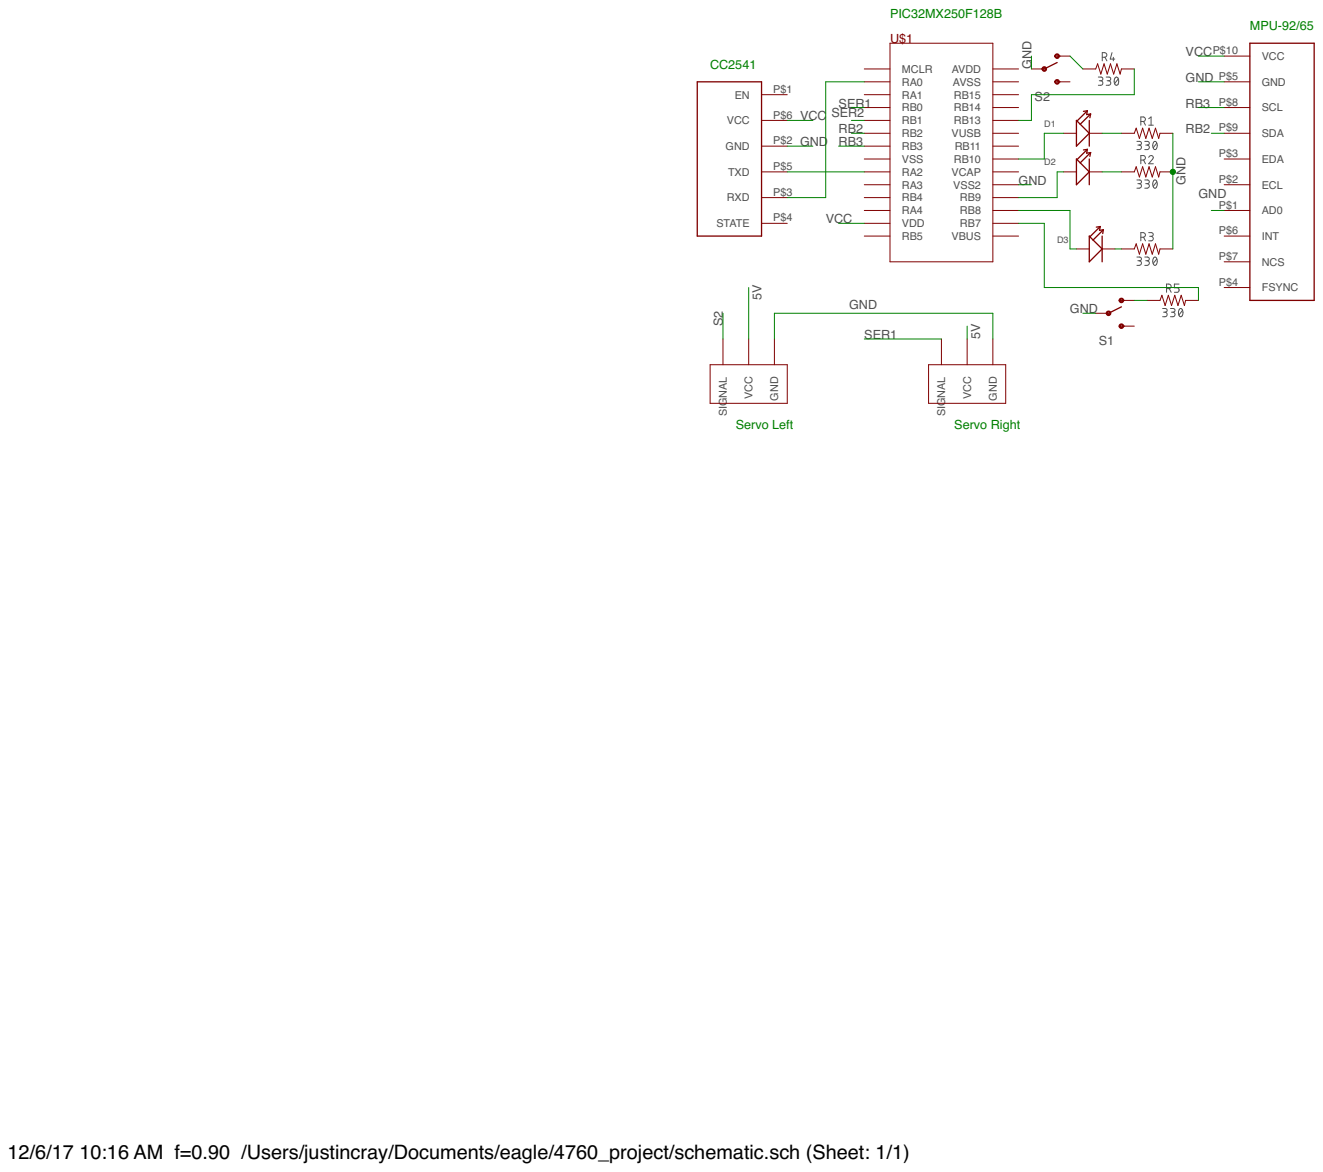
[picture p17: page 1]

AVSS RB15 RB14 RB13 VUSB RB11 RB10 VCAP RB9 RB8 VSS2 RB7 VBUS

12/6/17 10:16 AM f=0.90 /Users/justincray/Documents/eagle/4760_project/schematic.sch (Sheet: 1/1)

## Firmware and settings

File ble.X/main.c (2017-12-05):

#include "main.h"
#include "ble.h"
#include "config_1_2_2.h"
#include "pt_cornell_1_2_2.h"
//#include "segment_display.h"
#include "servo.h"
#include <stdlib.h>
#include "imu.h"
#include <limits.h>

#define TARGET_MAGIC_ID 2
const char *BLE_MACS[] = {"3CA30807276A", "3CA30807B62E", "3CA3080738E3"};
const char *BLE_NAMES[] = {"PIRATE", "EAGLE", "NYMERIA"};
#define OTHER_ADDR (BLE_MACS[TARGET_MAGIC_ID])
#define STR(s) #s
#define XSTR(s) STR(s)
#define MAGIC_BLE_NAME(ID) (BLE_NAMES[ID])
#define SPEED 10
#define QUANTA 500
#define SEGMENTS 20 
#define SHORTDRIVE 20
#define END_RSSI (-40)
#define TURN_THRESHOLD 30
#define CALIB_TIME 7000
#define TURN_TIMEOUT 2000
#define ALPHA 0.2

#define LED_PORTA IOPORT_B
#define LED_PINA BIT_8
#define LED_PORTB IOPORT_B
#define LED_PINB BIT_9
#define LED_PORTC IOPORT_B
#define LED_PINC BIT_10

#define SW_PORT0 IOPORT_B
#define SW_PIN0 BIT_7
#define SW_PORT1 IOPORT_B
#define SW_PIN1 BIT_13

#define COMMAND_DELAY 100

static int lastturn = 0;

static pt_t pt_blinky, pt_ble, pt_ble_receive;

static int my_id;

static int get_id() {
    PORTSetPinsDigitalIn(SW_PORT0, SW_PIN0);
    PORTSetPinsDigitalIn(SW_PORT1, SW_PIN1);
    CNPUB = SW_PIN0 | SW_PIN1;
    CNPDB = 0;

    char bit_0 = PORTReadBits(SW_PORT0, SW_PIN0) == 0;
    char bit_1 = PORTReadBits(SW_PORT1, SW_PIN1) == 0;

    my_id = bit_1 << 1 | bit_0;
    return my_id;
}

static PT_THREAD(blinky(struct pt *pt)) {
    static char buf[500];
    PT_BEGIN(pt);

    //    PORTClearBits(LED_PORTA, LED_PINA);
    //    PORTClearBits(LED_PORTB, LED_PINB);
    //    PORTClearBits(LED_PORTC, LED_PINC);

    //    PORT_WRITE(LED_PORTA, LED_PINA, my_id & (0x1 << 0));
    //    PORT_WRITE(LED_PORTB, LED_PINB, my_id & (0x1 << 1));

    while (my_id == TARGET_MAGIC_ID) {
        PT_YIELD_TIME_msec(250);
        PORT_WRITE(LED_PORTC, LED_PINC, 0);
        PT_YIELD_TIME_msec(250);
        PORT_WRITE(LED_PORTC, LED_PINC, 1);
    }
    PORT_WRITE(LED_PORTC, LED_PINC, 1);
    PT_END(pt);
}

static PT_THREAD(drive(struct pt *pt, int rssi)) {
    static int last_rssi;
    static int state;
    static char buf[500];
    static int i;
    static int start_heading, goal_heading;
    static int left;
    static int straight_time;
    static unsigned int timestamp;
    PT_BEGIN(pt);


    sprintf(buf, "IMU reading: %d", imu_get_heading());
    BLE_UART_PRINTLN(pt, COM_UART, buf);

    if (last_rssi == 0) {
        servo_drive(20, 0);
        state = 0b11;
    } else if (rssi != 0) {
        if (rssi > last_rssi) {
            state = 0b00;
            sprintf(buf, "SERVO straight");
            BLE_UART_PRINTLN(pt, COM_UART, buf);
            straight_time = QUANTA;
        } else {
            //            if (lastturn) {
            //                lastturn = 0;
            //                left = 2;
            //            } else
            if (rand() & 0x01) {
                left = 1;
                state = 0b01;
                lastturn = 1;
            } else {
                left = -1;
                state = 0b10;
                lastturn = 1;
            }
            start_heading = imu_get_heading();
            goal_heading = degree(start_heading + left * 90);

            sprintf(buf, "SERVO turn; start: %d, goal: %d left: %d, fun: %d", start_heading, goal_heading, left, start_heading + left * 90);
            BLE_UART_PRINTLN(pt, COM_UART, buf);


            timestamp = PT_GET_TIME();
            while (abs(angle_diff(imu_get_heading(), goal_heading)) > TURN_THRESHOLD && PT_GET_TIME() - timestamp < TURN_TIMEOUT) {
                //                sprintf(buf, "IMU curr: %d, goal: %d angle diff: %d,", imu_get_heading(), goal_heading, angle_diff(imu_get_heading(), goal_heading));
                //                BLE_UART_PRINTLN(pt, COM_UART, buf);
                servo_drive(SPEED * 2, left * 100);
                PT_YIELD(pt);
            }
            sprintf(buf, "SERVO turn end: heading: %d", imu_get_heading());
            BLE_UART_PRINTLN(pt, COM_UART, buf);

            sprintf(buf, "SERVO done turning");
            BLE_UART_PRINTLN(pt, COM_UART, buf);

            servo_drive(0, 0);
            PT_YIELD_TIME_msec(100);
            straight_time = QUANTA / 2;
        }

        start_heading = imu_get_heading();
        for (i = 0; i < SEGMENTS; i++) {
            servo_drive_straight(SPEED, start_heading);
            if (straight_time == QUANTA) {
                PT_YIELD_TIME_msec(straight_time / SEGMENTS / 2);
            } else {
                PT_YIELD_TIME_msec(straight_time / SEGMENTS * 2);
            }
        }
        //        servo_drive(SPEED, 0);
        PT_YIELD_TIME_msec(straight_time);
    }


    last_rssi = rssi;
    servo_drive(0, 0);

    PORT_WRITE(LED_PORTA, LED_PINA, state & (0x1 << 0));
    PORT_WRITE(LED_PORTB, LED_PINB, state & (0x1 << 1));
    PT_END(pt);
}

static PT_THREAD(ble1(struct pt *pt)) {
    static char buf[500];
    static int i;
    static char* ROLE_STRING;
    static char* IMME_STRING;
    static pt_t pt_drive;
    static int rssi_1;
    static int rssi_2;
    static int mag[3];
    static unsigned int start_time;
    static int lastx, lasty;
    PT_BEGIN(pt);

    sprintf(buf, "Hello World");
    BLE_UART_PRINTLN(pt, COM_UART, buf);
    PT_YIELD_TIME_msec(COMMAND_DELAY);

    start_time = PT_GET_TIME();

    //    xmax = 40;
    //    xmin = -10;
    //    ymax = 50;
    //    ymin = -10;
    xmax = INT_MIN;
    xmin = INT_MAX;
    ymax = INT_MIN;
    ymin = INT_MAX;

    while (PT_GET_TIME() < start_time + CALIB_TIME) {
        servo_drive(SPEED, 100);

        imu_mag_read_data(mag);

        lastx = mag[0] * ALPHA + lastx * (1 - ALPHA);
        lasty = mag[1] * ALPHA + lasty * (1 - ALPHA);

        if (lastx > xmax) xmax = lastx;
        if (lastx < xmin) xmin = lastx;
        if (lasty > ymax) ymax = lasty;
        if (lasty < ymin) ymin = lasty;
    }
    sprintf(buf, "xmax %d xmin %d ymax %d ymin %d", xmax, xmin, ymax, ymin);
    BLE_UART_PRINTLN(pt, COM_UART, buf);
    servo_drive(0, 0);

    BLE_UART_PRINTLN(pt, COM_UART, "Configuring Chip");
    PT_YIELD_TIME_msec(COMMAND_DELAY);


    BLE_UART_PRINTLN(pt, BLE_UART, "AT+RESET");
    BLE_UART_PRINTLN(pt, COM_UART, "AT+RESET");
    PT_YIELD_TIME_msec(COMMAND_DELAY);

    BLE_UART_PRINTLN(pt, BLE_UART, "AT+IBEA1");
    BLE_UART_PRINTLN(pt, COM_UART, "AT+IBEA1");
    PT_YIELD_TIME_msec(COMMAND_DELAY);
    BLE_UART_PRINTLN(pt, BLE_UART, "AT+IBEA?");
    BLE_UART_PRINTLN(pt, COM_UART, "AT+IBEA?");
    PT_YIELD_TIME_msec(COMMAND_DELAY);

    ROLE_STRING = my_id == TARGET_MAGIC_ID ? "AT+ROLE0" : "AT+ROLE1";

    BLE_UART_PRINTLN(pt, BLE_UART, ROLE_STRING);
    BLE_UART_PRINTLN(pt, COM_UART, ROLE_STRING);
    PT_YIELD_TIME_msec(COMMAND_DELAY);
    BLE_UART_PRINTLN(pt, BLE_UART, "AT+ROLE?");
    BLE_UART_PRINTLN(pt, COM_UART, "AT+ROLE?");
    PT_YIELD_TIME_msec(COMMAND_DELAY);

    IMME_STRING = my_id == TARGET_MAGIC_ID ? "AT+IMME0" : "AT+IMME1";

    BLE_UART_PRINTLN(pt, BLE_UART, IMME_STRING);
    BLE_UART_PRINTLN(pt, COM_UART, IMME_STRING);
    PT_YIELD_TIME_msec(COMMAND_DELAY);
    BLE_UART_PRINTLN(pt, BLE_UART, "AT+IMME?");
    BLE_UART_PRINTLN(pt, COM_UART, "AT+IMME?");
    PT_YIELD_TIME_msec(COMMAND_DELAY);

    sprintf(buf, "AT+NAME%s", MAGIC_BLE_NAME(my_id));
    BLE_UART_PRINTLN(pt, BLE_UART, buf);
    BLE_UART_PRINTLN(pt, COM_UART, buf);
    PT_YIELD_TIME_msec(COMMAND_DELAY);
    BLE_UART_PRINTLN(pt, BLE_UART, "AT+NAME?");
    BLE_UART_PRINTLN(pt, COM_UART, "AT+NAME?");
    PT_YIELD_TIME_msec(COMMAND_DELAY);
    BLE_UART_PRINTLN(pt, BLE_UART, "AT+SHOW3");
    BLE_UART_PRINTLN(pt, COM_UART, "AT+SHOW3");
    PT_YIELD_TIME_msec(COMMAND_DELAY);
    BLE_UART_PRINTLN(pt, BLE_UART, "AT+SHOW?");
    BLE_UART_PRINTLN(pt, COM_UART, "AT+SHOW?");
    PT_YIELD_TIME_msec(COMMAND_DELAY);
    BLE_UART_PRINTLN(pt, BLE_UART, "AT+ADDR?");
    BLE_UART_PRINTLN(pt, COM_UART, "AT+ADDR?");
    PT_YIELD_TIME_msec(COMMAND_DELAY);
    BLE_UART_PRINTLN(pt, COM_UART, "=====================");

    while (1) {
        ble_enable_capture("OK+DISCE");
        BLE_UART_PRINTLN(pt, BLE_UART, "AT+DISI?");
        BLE_WAIT_FOR_CAPTURE(pt);
        ble_disable_capture();
        rssi_1 = ble_rssi_from_capture(OTHER_ADDR);
        ble_enable_capture("OK+DISCE");
        BLE_UART_PRINTLN(pt, BLE_UART, "AT+DISI?");
        BLE_WAIT_FOR_CAPTURE(pt);
        ble_disable_capture();
        rssi_2 = ble_rssi_from_capture(OTHER_ADDR);

        rssi_2 = (rssi_1 + rssi_2) / 2;
        sprintf(buf, "RSSI: %03d", rssi_2);
        BLE_UART_PRINTLN(pt, COM_UART, buf);
        if (rssi_2 < END_RSSI) {
            PT_SPAWN(pt, &pt_drive, drive(&pt_drive, rssi_2));
        } else { //goal reached, blinky celebration
            while (1) {
                PORT_WRITE(LED_PORTC, LED_PINC, rand() & 0x01);
                PORT_WRITE(LED_PORTA, LED_PINA, rand() & 0x01);
                PORT_WRITE(LED_PORTB, LED_PINB, rand() & 0x01);
                PT_YIELD_TIME_msec(500);
            }
        }
    }
    PT_END(pt);
}

int main() {
    PT_setup();
    PT_INIT(&pt_blinky);
    PT_INIT(&pt_ble);
    PT_INIT(&pt_ble_receive);

    INTEnableSystemMultiVectoredInt();

    ble_init();
    get_id();
    if (my_id != TARGET_MAGIC_ID) {
        servo_init();
        imu_init();
    }

    servo_set(0, 0);

    PORTSetPinsDigitalOut(LED_PORTA, LED_PINA);
    PORTSetPinsDigitalOut(LED_PORTB, LED_PINB);
    PORTSetPinsDigitalOut(LED_PORTC, LED_PINC);

    //    SEGMENT_DISPLAY_OPEN();
    //    SEGMENT_DISPLAY_NUMBER(0);

    while (1) {
        PT_SCHEDULE(blinky(&pt_blinky));
        PT_SCHEDULE(ble1(&pt_ble));
        PT_SCHEDULE(ble_receive((&pt_ble_receive)));
    }
}

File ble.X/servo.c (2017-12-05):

#include "servo.h"
#include "pt_cornell_1_2_2.h"
#include "imu.h"

#include <math.h>
#include <stdlib.h>

#define MIN_PWM_VALUE 1280
#define MAX_PWM_VALUE 2560
#define ZERO_PWM_VALUE 1880 //1920 //((MAX_PWM_VALUE - MIN_PWM_VALUE) / 2 + MIN_PWM_VALUE)
#define ZERO_PWM_RANGE (MAX_PWM_VALUE - ZERO_PWM_VALUE)

#define IMU_NOISE 5
#define IMU_BUFSIZE 5
static int heading_buf[IMU_BUFSIZE];

void servo_raw_set_1(int val) {
    SetDCOC3PWM(val);
}

void servo_raw_set_2(int val) {
    SetDCOC2PWM(val);
}

int servo_norm_to_raw(int val) {
    if (val == 0) {
        return 0;
    }
    int result = val * ZERO_PWM_RANGE / 100 + ZERO_PWM_VALUE;
    if (result > ZERO_PWM_VALUE + ZERO_PWM_RANGE) {
        result = ZERO_PWM_VALUE + ZERO_PWM_RANGE;
    }
    if (result < ZERO_PWM_VALUE - ZERO_PWM_RANGE) {
        result = ZERO_PWM_VALUE - ZERO_PWM_RANGE;
    }
    return result;
}

void servo_set_1(int val) {
    servo_raw_set_1(servo_norm_to_raw(val));
}

void servo_set_2(int val) {
    servo_raw_set_2(servo_norm_to_raw(val));
}

void servo_set(int left, int right) {
    servo_set_2(left);
    servo_set_1(-right);
}

void servo_drive(int power, int twist) {
    servo_set(power + power * twist / 100, power - power * twist / 100);
}

int servo_drive_straight(int speed, double fwd_heading) {
    int left = speed * 4;
    int right = speed * 4;
    int curr_heading = imu_get_heading();

//    if (angle_diff(curr_heading, fwd_heading) < -IMU_NOISE) {
//        left /= 2;
//    } else if (angle_diff(curr_heading, fwd_heading) > IMU_NOISE) {
//        right /= 2;
//    } // else, left and right stay the same  
    servo_set(left, right*1.5);
}
//Nothing

void __ISR(_TIMER_2_VECTOR, IPL2AUTO) Timer2Handler(void) {
    mT2ClearIntFlag();
}

void servo_init() {
    OpenTimer2(T2_ON | T2_SOURCE_INT | T2_PS_1_32, 25600);
    ConfigIntTimer2(T2_INT_ON | T2_INT_PRIOR_2);

    mT2ClearIntFlag();

    // set up compare3 for PWM mode
    OpenOC3(OC_ON | OC_TIMER2_SRC | OC_PWM_FAULT_PIN_DISABLE, 0, 0);
    OpenOC2(OC_ON | OC_TIMER2_SRC | OC_PWM_FAULT_PIN_DISABLE, 0, 0);

    PPSOutput(4, RPB0, OC3);
    PPSOutput(2, RPB1, OC2);

    // initialize random
    int i;
    for (i = 0; i < IMU_BUFSIZE; i++) {
        heading_buf[i] = (rand() & 0x1FF) % 360 - 180;
    }
}

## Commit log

2017-12-05 generate cad renderings
    [drag.scad, main.scad, wheel.scad]
2017-12-05 make cad look nice
2017-12-05 regulatory stuff
2017-12-06 imu stuff
2017-12-06 imu picture
2017-12-06 added servos and more bluetooth to testing
2017-12-06 broken i2c links fixed
2017-12-06 added servo description
2017-12-06 servo timer stuff
2018-02-02 Schematic with small dev board
    [bluehunters.sch]
2018-02-02 Add VIN
    [bluehunters.sch]
2018-02-03 incorperate schematics
2018-02-03 Fix switches in schematics
    [bluehunters.sch]
2018-02-05 add battery to schem
    [bluehunters.sch]
2018-02-06 10 trial data
    [timetest.csv]
2018-02-06 put in updated csv
    [timetest.csv]
